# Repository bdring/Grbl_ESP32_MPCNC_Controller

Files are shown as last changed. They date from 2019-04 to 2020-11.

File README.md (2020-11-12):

# MPCNC Grbl_ESP32 Controller

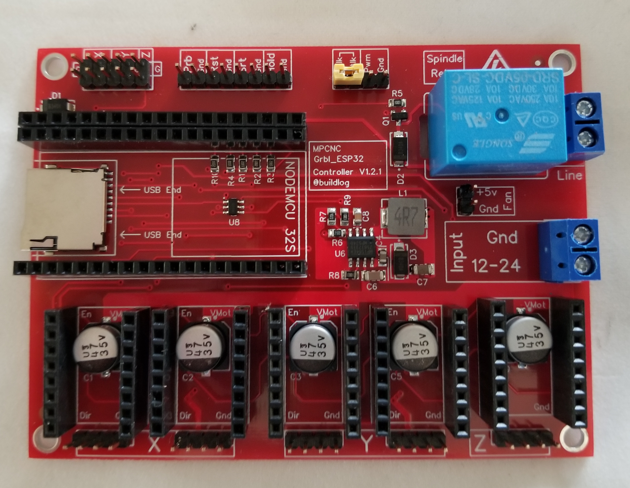
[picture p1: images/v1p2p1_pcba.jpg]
MPCNC Controller Image


This is a CNC controller specially designed to address the needs of the [MPCNC (Mostly Printed CNC) CNC Router](https://www.v1engineering.com/specifications/).

### Features

- ESP32 Microcontroller:
  - Very Fast: Dual core 32 bit, 240 MHz
  - Large Flash Memory
  - Wifi:
  - Bluetooth:
- Grbl_ESP32 Firmware:
  - Compatible with most existing Grbl gcode sender software.
  - Web User Interface
  - Multiple Interfaces
    - USB Serial:
    - Web User Interface:
    - Telnet:
    - Bluetooth:
    - SD Card:
- (5) Stepper Motor Drivers: On for each motor in the MPCNC design. Motors are ganging in firmware and have an auto squaring feature executed during homing.
- Limit Switch Connectors: 
- Control Pins:
- Spindle Control:
- Fan Power: 
- Micro SD card: 

### Getting One

They are available at the following links or you can source it yourself.

- [Tindie](https://www.tindie.com/products/33366583/grbl_esp32-mpcnc-cnc-controller/)

### Usage Instructions

[See the wiki](https://github.com/bdring/Grbl_ESP32_MPCNC_Controller/wiki)

### License

Creative Commons Attribution - ShareAlike 4.0 International

There are no commercial restrictions on using this design, but you must attribute the design to Bart Dring or @buildlog. You must also publish any changes or improvements to the design with the same open source license.  

### Version History

- Version 1.1 Original upload
- Version 1.2
  - Removed R/C filters on limit switches. This was not working for everyone. A firmware debouncing feature was added.
  - Made GPIO2 and output. Some dev modules have trouble with this as an input. Shuffled a few pins to accomodate this change. 
- Version 1.2.1
  - Changed orientation of relay for better layout
  - Removed pull down resistor on spindle PWM circuit (it was never installed previously)
  - Note: This uses the same cpu_map ans V1.2

### Source Files

- [Firmware](https://github.com/bdring/Grbl_Esp32)
- [DipTrace Source](https://github.com/bdring/Grbl_ESP32_MPCNC_Controller/tree/master/source)
- [Gerber Files](https://github.com/bdring/Grbl_ESP32_MPCNC_Controller/tree/master/gerbers)
- [Schematic](https://github.com/bdring/Grbl_ESP32_MPCNC_Controller/blob/master/gerbers/schematic.pdf)

### Donation

This project requires a lot of work and often expensive items for testing. Please consider a safe, secure and highly appreciated donation via the PayPal link below.



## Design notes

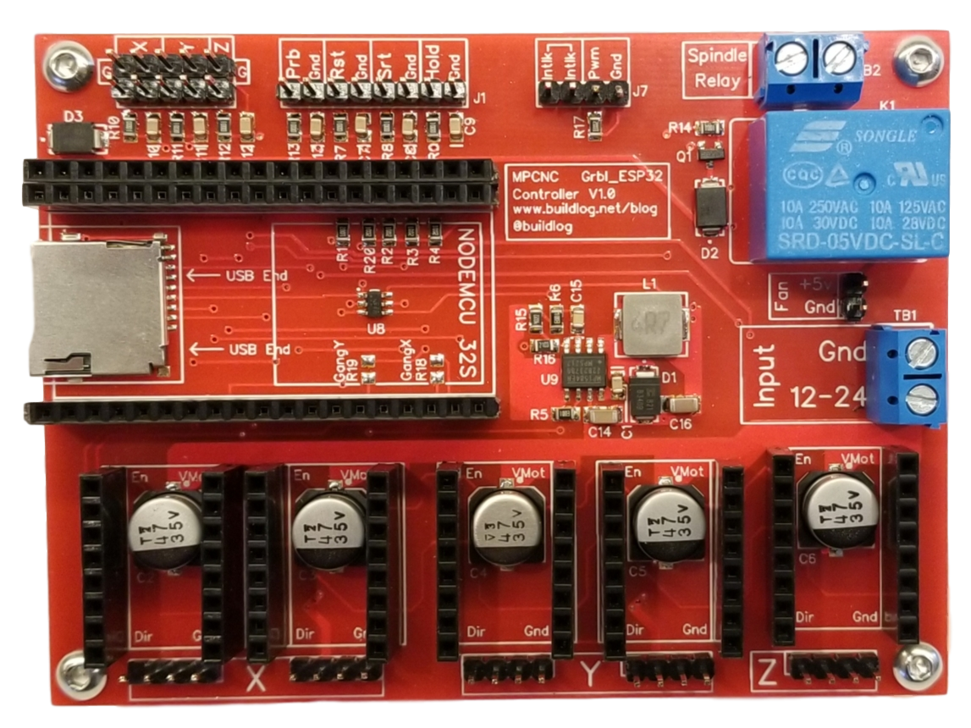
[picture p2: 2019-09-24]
images/v1p2_pcba.png

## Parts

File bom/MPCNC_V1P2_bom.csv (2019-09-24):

RefDes | Description | Value | Manufacturer | Mfg P/N | Link
C1, C2, C3, C5, C9 | Capacitor, Electrolytic | 47u 35V | Nichicon | UWX1V470MCL1GB | https://www.digikey.com/short/p80qq5
C1 | Capacitor, Ceramic | 100nF 50V | Kemet | C0805C104K5RACAUTO | https://lcsc.com/product-detail/Multilayer-Ceramic-Capacitors-MLCC-SMD-SMT_KEMET_C0805C104K5RACAUTO_100nF-104-10-50V-Car-level_C129641.html
C7 | Capacitor, Ceramic | 22uF 6.3V | Taiyo Yuden | JMK316BJ226KL-T | https://lcsc.com/product-detail/Multilayer-Ceramic-Capacitors-MLCC-SMD-SMT_TAIYO-YUDEN_JMK316BJ226KL-T_22uF-226-10-6-3V_C92791.html
C8 | Capacitor, Ceramic | 10uF | Taiyo Yuden | GMK316BJ106KL-T | https://lcsc.com/product-detail/Multilayer-Ceramic-Capacitors-MLCC-SMD-SMT_Taiyo-Yuden-GMK316BJ106KL-T_C92797.html
C15 | Capacitor, Ceramic | 150pF 50v 0805 | CCTC | TCC0805X7R151K500BT | https://lcsc.com/product-detail/Multilayer-Ceramic-Capacitors-MLCC-SMD-SMT_CCTC-TCC0805X7R151K500BT_C282743.html
D1, D2, D3 | Diode, Schottkey | diode, Schottkey 3A | (MDD) Jiangsu Yutai Elec | (MDD) Jiangsu Yutai Elec | https://lcsc.com/product-detail/Schottky-Barrier-Diodes-SBD_Jiangsu-Yutai-Elec-B340A_C64982.html
J1 | Connector, Header | Header Male 1x8 0.1" | Nextronics Engineering | Z-211-0811-0021-001 | https://lcsc.com/product-detail/Others_Nextronics-Engineering-Z-211-0811-0021-001_C190820.html
J2, J4, J6, J7, J9, J11 | Connector, Header | Header Male 1x4 0.1" | TE Connectivity |  | https://lcsc.com/product-detail/Male-Header_2-54mm-1-4P-HeaderG-FRegular_C152150.html
J3 | Connector, Header | Header Male 2x5 0.1" | Nextronics Engineering | Z-21310110021001 | https://lcsc.com/product-detail/PCB-Connectors-Headers-Male-Pins_Nextronics-Engineering-Z-21310110021001_C115170.html
J8 | Connector, Header | Header Male 1x2 0.1" | Nextronics Engineering | Z-211-0211-0021-001 | https://lcsc.com/product-detail/Male-Header_2-54mm-1-2P-Header-G-FRegular_C152154.html
J10 | Socket, Micro SD | Micro SD Socket | Korean Hroparts Elec TF-01A | TF-01A | https://lcsc.com/product-detail/Connector-Card-Sockets_Korean-Hroparts-Elec-TF-01A_C91145.html
K1 | Relay | Relay 5V SPDT | Ningbo Songle Relay | SRD-05VDC-SL-C | https://lcsc.com/product-detail/Relays_SRD-05VDC-SL-C_C35449.html
L1 | Inductor | Inductor 4.7uH 5.5A | Chilisin Elec | MHCI06030-4R7M-R8 | https://lcsc.com/product-detail/Power-Inductors_Chilisin-Elec-MHCI06030-4R7M-R8_C108295.html
Q1 | Transistor | NPN Transistor 0.5A | Semtech | MMBT9013H | https://lcsc.com/product-detail/Transistors-NPN-PNP_MMBT9013H_C81408.html
R1, R2, R3, R4, R10 | Resistor | 10k | YAGEO | AC0805FR-0710KL | https://lcsc.com/product-detail/Chip-Resistor-Surface-Mount_10KR-1002-1_C140868.html
R5 | Resistor | 1K | YAGEO | AC0805FR-071KL | https://lcsc.com/product-detail/Chip-Resistor-Surface-Mount_1KR-1001-1_C140870.html
R6 | Resistor | 210k | YAGEO | AC0805FR-07210KL | https://lcsc.com/product-detail/Others_YAGEO-AC0805FR-07210KL_C228629.html
R7 | Resistor | 40.2k | YAGEO | AC0805FR-0740K2L | https://lcsc.com/product-detail/Others_YAGEO-AC0805FR-0740K2L_C228820.html
R8, R9 | Resistor | 100k | YAGEO | AC0805FR-07100KL | https://lcsc.com/product-detail/Chip-Resistor-Surface-Mount_100KR-1003-1_C144587.html
TB1, TB2 | Terminal Block | Terminal Block 1x2 5mm Blue | Aliexpress |  | https://www.aliexpress.com/item/Free-Shipping-5-08-301-2P-301-2P-500PCS-2-Pin-Screw-Terminal-Block-Connector-5mm/1681835880.html
U1, J9 | Connector, Header | ESP-32 Header Female 1x19 0.1" |  |  | https://www.aliexpress.com/item/100Pcs-Per-Lot-2-54mm-Pitch-1x19-Pin-19-Pin-Female-Single-Row-Straight-Header-Strip/32760221364.html
U2, U3, U4, U5, U7 | Connector, Header | Header Female 1x8 0.1" |  |  | https://lcsc.com/product-detail/Female-Header_2-54mm-1-8P-Straight-Female-header_C27438.html
U6 | DC-DC Power Supply Controller | MP1584EN | Monolithic Power Systems | MP1584EN-LF-Z | https://lcsc.com/product-detail/DC-DC-Converters_MPS_MP1584EN-LF-Z_MP1584EN-LF-Z_C15051.html
U8 | Voltage level Shifter | TXS0101DBVR | TI | TXS0101DBVR | https://lcsc.com/product-detail/Logic-ICs_TI_TXS0101DBVR_TXS0101DBVR_C132604.html

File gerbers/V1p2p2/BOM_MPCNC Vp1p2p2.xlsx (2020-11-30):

RefDes | Value | Quantity | SMD | Thru Hole | Manufacturer | Mfg P/n | Link
C1, C2, C3, C5, C9 | 47u 35V | 5 | 5 |  | Nichicon | UWX1V470MCL1GB | https://www.digikey.com/short/ptwvbr
C4, C10, C11, C12, C13, C14, C15, C16 | 100nF | 8 | 8 |  | Kemet | C0805C104K5RACAUTO | https://lcsc.com/product-detail/Multilayer-Ceramic-Capacitors-MLCC-SMD-SMT_KEMET_C0805C104K5RACAUTO_100nF-104-10-50V-Car-level_C129641.html
C6 | 10uF | 1 | 1 |  | Taiyo Yuden | GMK316BJ106KL-T | https://lcsc.com/product-detail/Multilayer-Ceramic-Capacitors-MLCC-SMD-SMT_Taiyo-Yuden-GMK316BJ106KL-T_C92797.html
C7 | 22uF 6.3V | 1 | 1 |  | Taiyo Yuden | JMK316BJ226KL-T | https://lcsc.com/product-detail/Multilayer-Ceramic-Capacitors-MLCC-SMD-SMT_TAIYO-YUDEN_JMK316BJ226KL-T_22uF-226-10-6-3V_C92791.html
C8 | 150pF | 1 | 1 |  | CCTC | TCC0805X7R151K500BT | https://lcsc.com/product-detail/Multilayer-Ceramic-Capacitors-MLCC-SMD-SMT_CCTC-TCC0805X7R151K500BT_C282743.html
D1, D2, D3 | Diode, Schottkey 3A | 3 | 3 |  | (MDD) Jiangsu Yutai Elec | (MDD) Jiangsu Yutai Elec | https://lcsc.com/product-detail/Schottky-Barrier-Diodes-SBD_Jiangsu-Yutai-Elec-B340A_C64982.html
J1 | Header Male 1x8 0.1" | 1 |  | 1 | Nextronics Engineering | Z-211-0811-0021-001 | https://lcsc.com/product-detail/Others_Nextronics-Engineering-Z-211-0811-0021-001_C190820.html
J2, J4, J6, J7, J9, J11 | Header Male 1x4 0.1" | 5 |  | 5 |  |  | https://lcsc.com/product-detail/Male-Header_2-54mm-1-4P-HeaderG-FRegular_C152150.html
J3 | Header Male 2x5 0.1" | 1 |  | 1 | MINTRON | MTP125-1205S1 | https://lcsc.com/product-detail/Pin-Header-Female-Header_MINTRON-MTP125-1205S1_C358694.html
J8 | Male Header 1x2 0.1" | 1 |  | 1 | MINTRON | MTP125-1102S1 | https://lcsc.com/product-detail/Pin-Header-Female-Header_MINTRON-MTP125-1102S1_C358684.html
J10 | Micro SD Socket | 1 |  | 1 | Korean Hroparts Elec TF-01A | TF-01A | https://lcsc.com/product-detail/Connector-Card-Sockets_Korean-Hroparts-Elec-TF-01A_C91145.html
K1 | Relay 5VDC SPDT | 1 |  | 1 | Ningbo Songle Relay | SRD-05VDC-SL-C | https://lcsc.com/product-detail/Relays_Ningbo-Songle-Relay-SRD-05VDC-SL-C_C35449.html
L1 | 4.7uH | 1 | 1 |  | Chilisin Elec | MHCI06030-4R7M-R8 | https://lcsc.com/product-detail/Power-Inductors_Chilisin-Elec-MHCI06030-4R7M-R8_C108295.html
Q1 |  | 1 | 1 |  | Nexperia | BCV26,215 | https://lcsc.com/product-detail/Darlington-Transistors_Nexperia_BCV26-215_BCV26-215_C130420.html
R1, R2, R3, R4, R10 | 10k | 5 | 5 |  | YAGEO | AC0805FR-0710KL | https://lcsc.com/product-detail/Chip-Resistor-Surface-Mount_10KR-1002-1_C140868.html
R5 | 1K | 1 | 1 |  | YAGEO | AC0805FR-071KL | https://lcsc.com/product-detail/Chip-Resistor-Surface-Mount_1KR-1001-1_C140870.html
R6 | 210k | 1 | 1 |  | YAGEO | AC0805FR-07210KL | https://lcsc.com/product-detail/Others_YAGEO-AC0805FR-07210KL_C228629.html
R7 | 40.2k | 1 | 1 |  | YAGEO | AC0805FR-0740K2L | https://lcsc.com/product-detail/Others_YAGEO-AC0805FR-0740K2L_C228820.html
R8, R9 | 100k | 2 | 2 |  | YAGEO | AC0805FR-07100KL | https://lcsc.com/product-detail/Chip-Resistor-Surface-Mount_100KR-1003-1_C144587.html
R11, R12, R13, R14, R15, R16, R17 | 100R | 7 | 7 |  | YAGEO | AC0805FR-07100RL | https://lcsc.com/product-detail/Chip-Resistor-Surface-Mount_100R-100R-1_C138274.html
TB1, TB2 |  | 2 |  | 2 | DIBO | DB301V-5.0-2P | https://lcsc.com/product-detail/Screw-terminal_DIBO-DB301V-5-0-2P_C395882.html
U1,J5 | 1x19 Female Header 8.5mm Tall | 3 |  | 3 | 1x19 Female Header |  | https://www.aliexpress.com/item/100Pcs-Per-Lot-2-54mm-Pitch-1x19-Pin-19-Pin-Female-Single-Row-Straight-Header-Strip/32760221364.html
U2, U3, U4, U5, U7 | 1x8 Female Header 8.5mm Tall | 10 |  | 10 | 1x8 Female Header |  | https://lcsc.com/product-detail/Female-Header_2-54mm-1-8P-Straight-Female-header_C27438.html
U6 | MP1584EN | 1 | 1 |  | Monolithic Power Systems | MP1584EN-LF-Z | https://lcsc.com/product-detail/DC-DC-Converters_MPS_MP1584EN-LF-Z_MP1584EN-LF-Z_C15051.html
U8 | TXS0101DBVR | 1 | 1 |  | TI | TXS0101DBVR | https://lcsc.com/product-detail/Logic-ICs_TI_TXS0101DBVR_TXS0101DBVR_C132604.html
 |  |  | 40 | 25

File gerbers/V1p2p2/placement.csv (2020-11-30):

RefDes | Name | Pattern | X (in) | Y (in) | Side | Rotate | Value
C1 |  | CAPAE-8.35x8.35h6.2 | 0.55 | 0.774 | Top | 270 | 47u 35V
C2 |  | CAPAE-8.35x8.35h6.2 | 1.25 | 0.774 | Top | 270 | 47u 35V
C3 |  | CAPAE-8.35x8.35h6.2 | 2 | 0.774 | Top | 270 | 47u 35V
C4 | CAP_0805 | CAP_0805 | 2.4927 | 1.3852 | Top | 270 | 100nF
C5 |  | CAPAE-8.35x8.35h6.2 | 2.7 | 0.774 | Top | 270 | 47u 35V
C6 | CAP_NP_1206 | CAP_1206 | 2.4266 | 1.2567 | Top | 180 | 10uF 35V
C7 | CAP_NP_1206 | CAP_1206 | 2.7676 | 1.3 | Top | 0 | 22uF 6.3V
C8 | CAP_NP_1206 | CAP_0805 | 2.3167 | 1.675 | Top | 90 | 150pF
C9 |  | CAPAE-8.35x8.35h6.2 | 3.45 | 0.824 | Top | 270 | 47u 35V
D1 | 10BQ100 | b340a-13-f | 0.1699 | 2.4641 | Top | 0
D2 | 10BQ100 | b340a-13-f | 2.6188 | 2.16 | Top | 90
D3 | 10BQ100 | b340a-13-f | 2.6097 | 1.3578 | Top | 270
FD1 | Fiducial-1-3mm | Fiducial-1-3mm | 0.1378 | 0.315 | Top | 90
FD2 | Fiducial-1-3mm | Fiducial-1-3mm | 3.622 | 2.7756 | Top | 90
J1 | HDR-1x8 | HDR-1x8 | 1.45 | 2.65 | Top | 0 | Header Male 1x8 0.1
J2 |  | HDR-1x4 | 0.55 | 0.15 | Top | 0 | Header Male 1x4 0.1
J3 | HDR-2x5 | HDR-2x5 | 0.6 | 2.7 | Top | 0 | Header Male 2x5 0.1
J4 |  | HDR-1x4 | 1.25 | 0.15 | Top | 0 | Header Male 1x4 0.1
J5 | HDR-1x19 | HDR-1x19 | 1 | 2.3 | Top | 0
J6 |  | HDR-1x4 | 2 | 0.15 | Top | 0 | Header Male 1x4 0.1
J7 |  | HDR-1x4 | 2.7 | 0.15 | Top | 0 | Header Male 1x4 0.1
J8 | HDR-1x2 | HDR-1x2 | 3.075 | 1.7813 | Top | 270 | Header Male 1x2 0.1
J9 |  | HDR-1x4 | 3.425 | 0.15 | Top | 0 | Header Male 1x4 0.1
J10 | TF-01A | TF-01A | 0.3006 | 1.752 | Top | 0 | Micro SD Socket
J11 |  | HDR-1x4 | 2.35 | 2.65 | Top | 0 | Header Male 1x4 0.1
K1 | JS-M1-9V-5 | JS-M | 3.1705 | 2.2519 | Top | 90 | Relay 5V SPDT
L1 | IND_1210 | Inductor 06030 | 2.6506 | 1.6614 | Top | 0 | 4.7uH
Q1 | MMBT9014 | TO-236 | 2.6188 | 2.3856 | Top | 180
R1 | RES_0805 | RES_0805 | 1.5 | 2.0626 | Top | 270 | 10k
R2 | RES_0805 | RES_0805 | 1.6 | 2.0626 | Top | 270 | 10k
R3 | RES_0805 | RES_0805 | 1.7 | 2.0626 | Top | 270 | 10k
R4 | RES_0805 | RES_0805 | 1.4125 | 2.0624 | Top | 270 | 10k
R5 | RES_0805 | RES_0805 | 2.6124 | 2.4938 | Top | 0 | 1K
R6 | RES_0805 | RES_0805 | 2.1721 | 1.5596 | Top | 0 | 210k
R7 | RES_0805 | RES_0805 | 2.1347 | 1.6782 | Top | 270 | 40.2k
R8 | RES_0805 | RES_0805 | 2.2631 | 1.2606 | Top | 0 | 100k
R9 | RES_0805 | RES_0805 | 2.2257 | 1.675 | Top | 90 | 100k
R10 | RES_0805 | RES_0805 | 1.3 | 2.0624 | Top | 90 | 10k
TB1 | TB_5mm_2POS | TB_5mm_2POS | 3.8125 | 2.3438 | Top | 270
TB2 | TB_5mm_2POS | TB_5mm_2POS | 3.75 | 1.525 | Top | 270
U1 | ESP-32 NodeMCU 32S | ESP-32 NodeMCU 32S | 0.1 | 2.2 | Top | 270 | ESP-32
U2 | StepStick | StepStick | 0.3 | 1 | Top | 0
U3 | StepStick | StepStick | 1 | 1 | Top | 0
U4 | StepStick | StepStick | 1.75 | 1 | Top | 0
U5 | StepStick | StepStick | 2.45 | 1 | Top | 0
U6 | MP1584EN | MP1584EN | 2.3425 | 1.4551 | Top | 180 | MP1584EN
U7 | StepStick | StepStick | 3.2 | 1.05 | Top | 0
U8 | TXS0101DBVR | SOT23-6 | 1.4344 | 1.7501 | Top | 0 | TXS0101DBVR
C10 | CAP_0805 | CAP_0805 | 0.5 | 2.5187 | Top | 90 | 100nF
C11 | CAP_0805 | CAP_0805 | 0.7 | 2.5187 | Top | 90 | 100nF
C12 | CAP_0805 | CAP_0805 | 0.8938 | 2.5187 | Top | 90 | 100nF
R14 | RES_0805 | RES_0805 | 1.1 | 2.5187 | Top | 270 | 100
R15 | RES_0805 | RES_0805 | 1.3 | 2.5187 | Top | 270 | 100
R11 | RES_0805 | RES_0805 | 0.4 | 2.5187 | Top | 270 | 100
R12 | RES_0805 | RES_0805 | 0.6 | 2.5187 | Top | 270 | 100
R13 | RES_0805 | RES_0805 | 0.8 | 2.5187 | Top | 270 | 100
R16 | RES_0805 | RES_0805 | 1.5 | 2.5187 | Top | 270 | 100
R17 | RES_0805 | RES_0805 | 1.7 | 2.5187 | Top | 270 | 100
C13 | CAP_0805 | CAP_0805 | 1.2 | 2.5187 | Top | 90 | 100nF
C14 | CAP_0805 | CAP_0805 | 1.4 | 2.5187 | Top | 90 | 100nF
C15 | CAP_0805 | CAP_0805 | 1.6 | 2.5187 | Top | 90 | 100nF
C16 | CAP_0805 | CAP_0805 | 1.8 | 2.5187 | Top | 90 | 100nF

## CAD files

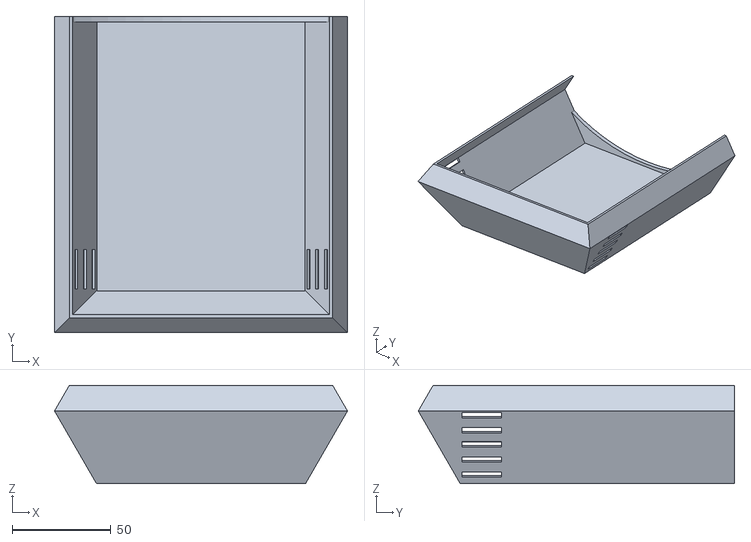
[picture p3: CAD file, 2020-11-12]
stl/Grbl_ESP-32 MPCNC Case Lid.stl
148.3 x 160.2 x 49.8

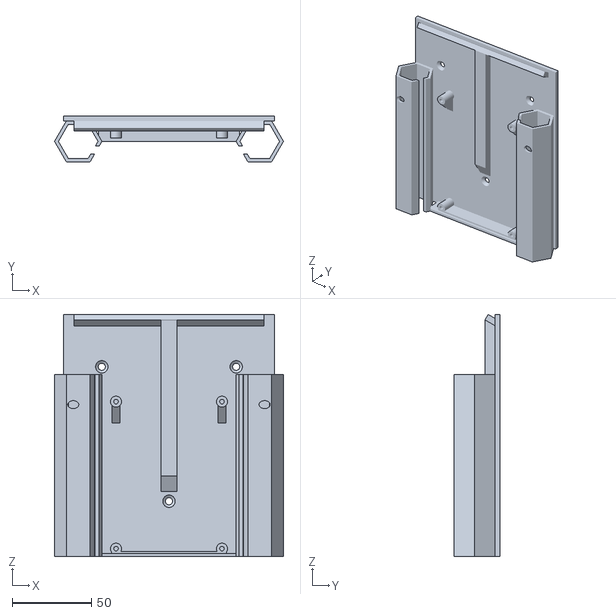
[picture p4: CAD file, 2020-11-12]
stl/Grbl_ESP-32 MPCNC Case Flat Base.stl
144.8 x 29.0 x 153.1

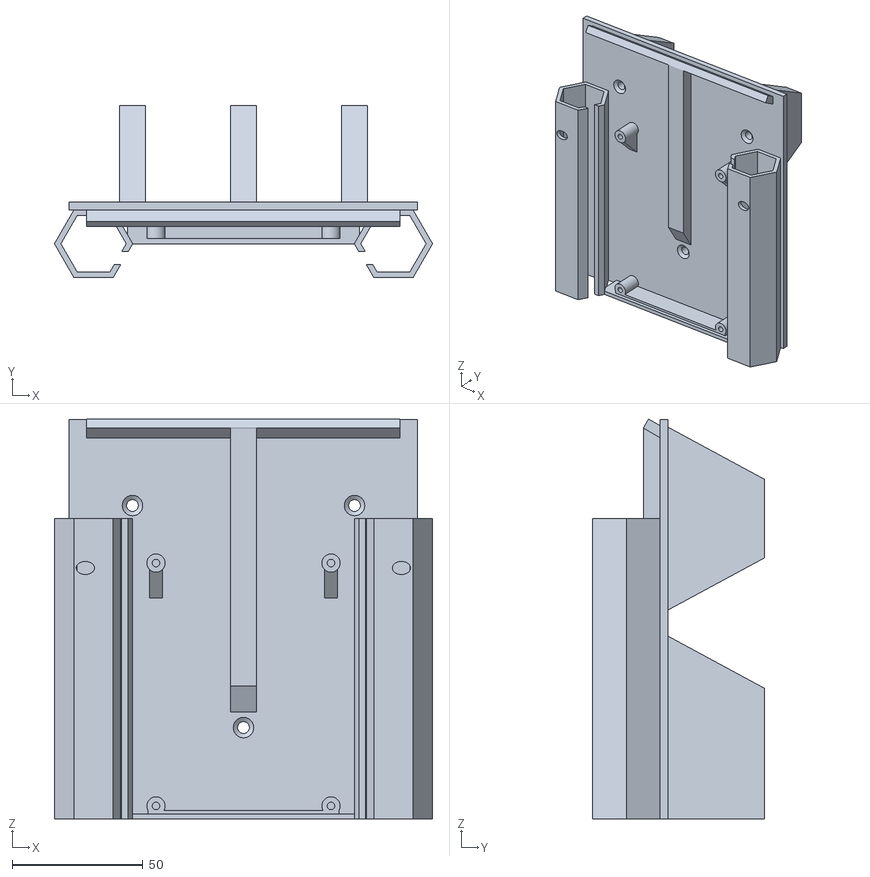
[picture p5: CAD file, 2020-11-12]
stl/Grbl_ESP-32 MPCNC Case Standoff Base.stl
144.8 x 66.0 x 153.1

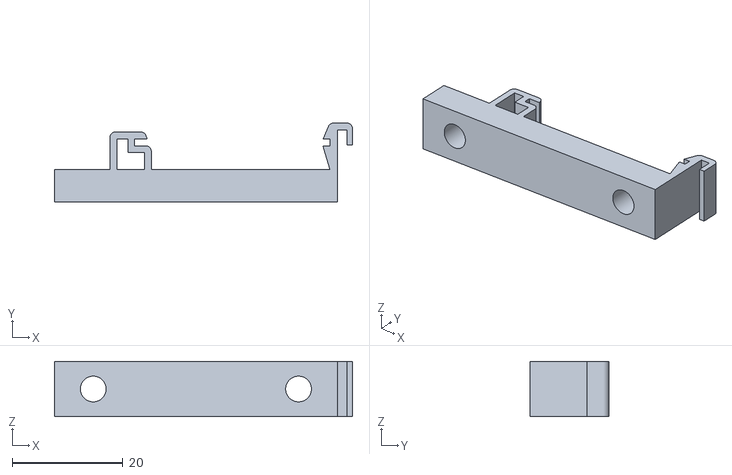
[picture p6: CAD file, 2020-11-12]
stl/DINRailClip.stl
53.8 x 14.3 x 10.0

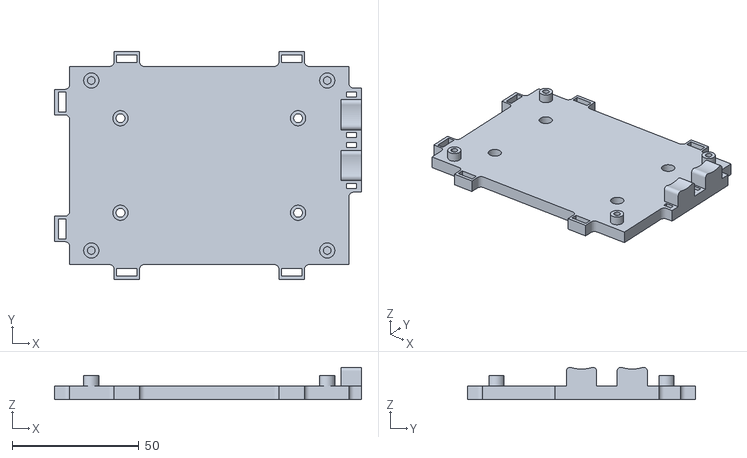
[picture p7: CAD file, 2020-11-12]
stl/GRBLESP32MPCNCDinRailPlate.stl
121.0 x 90.0 x 12.8

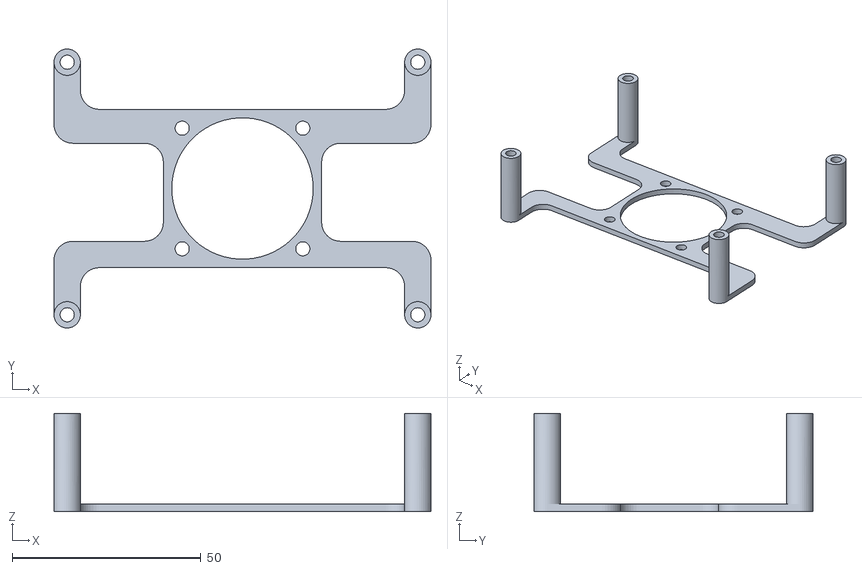
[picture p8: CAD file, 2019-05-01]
stl/mpcnc_fan_mount.stl
100.0 x 74.0 x 26.0

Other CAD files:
stl/Grbl_ESP-32 MPCNC Case Lid Holes.stl

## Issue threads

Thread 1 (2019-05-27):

Only one motor per axis moving

gmihovics, 2019-05-27:
I just finished wiring the four X and Y steppers and limit switches for my MPCNC. When trying to move either axis, only the second of the motors for that axis move. So if I move the X axis, only X2 moves, Y2 for Y.

I swapped the motors and drivers (A4988) to make sure all the components work and they do. I also went ahead and recompiled the firmware as per the wiki with no change.

I unfortunately do not have an oscilloscope or logic analyser so I can't verify the board is sending steps to both motors.

Am I overlooking something?

bdring, 2019-05-27:
My first guess is you are using the wrong cpu_map. You need to use CPU_MAP_MPCNC.

[See this page about that](https://github.com/bdring/Grbl_ESP32_MPCNC_Controller/wiki).

gmihovics, 2019-05-27:
Thanks for he quick reply. I unfortunately followed those instructions when I recompiled the firmware.

bdring, 2019-05-27:
I just checked the latest firmware to make sure there are no issues no issues crept in recent updates.

It works fine for me.  Can you double check all to solder joints?

You could try swapping the pins in cpu_map.h on the x axis motors to see if it is a firmware or hardware issue, like this....

#define X_STEP_PIN      GPIO_NUM_22   // was GPIO_NUM_12
#define X_STEP_B_PIN    GPIO_NUM_12 // was GPIO_NUM_22

If only one motors spins, but it is now the other one, it would appear to be a firmware issue.
If the same motors as before spins, it is likely a hardware issue.

gmihovics, 2019-05-27:
That's a good idea, I will try that when I get home today.

gmihovics, 2019-05-27:
So I have reconfigured the pins and uploaded the firmware like you suggested. I checked before and after and both times the same motor moved.

Here is the relevant code

`config.h`
```
#ifndef config_h
#define config_h
#include "grbl.h" // For Arduino IDE compatibility.

//#define ESP_DEBUG

// Define CPU pin map and default settings.
// NOTE: OEMs can avoid the need to maintain/update the defaults.h and cpu_map.h files and use only
// one configuration file by placing their specific defaults and pin map at the bottom of this file.
// If doing so, simply comment out these two defines and see instructions below.
#define DEFAULTS_GENERIC

//#define CPU_MAP_ESP32 // these are defined in cpu_map.h
#define CPU_MAP_MPCNC

#define VERBOSE_HELP // adds addition help info, but could confuse some senders
```

`cpu_map.h`
```
#define USE_GANGED_AXES // allow two motors on an axis

//#define X_STEP_PIN      GPIO_NUM_12
//#define X_STEP_B_PIN    GPIO_NUM_22	 // ganged motor
#define X_STEP_PIN GPIO_NUM_22 // was GPIO_NUM_12
#define X_STEP_B_PIN GPIO_NUM_12 // was GPIO_NUM_22

#define X_AXIS_SQUARING
```

I have also confirmed the the other motor works if i swap them as well as the drivers. The soldering looks well done, you sent a really nice board. I am not sure what is going on.

bdring, 2019-05-27:
Thanks for doing that. It helps narrow things down.  Does the non moving motor lock (resist manual turning) when the other motor moves?

Make sure $1=255 to keep it locked.

gmihovics, 2019-05-28:
Ok so interesting results. I verified $1 == 255. I also unplugged the good motors and told the board to move the X and Y axis. Like usual I got no movement but I can verify the other motors are energised. I am able to move them by hand but they have significant resistance compared to the unplugged motors and you can feel the skipping steps when you force them.

gmihovics, 2019-05-28:
I wrote a test program that stepped gpio 22 and it would spin the motor attached just fine. When I change it to pin 12, it does not.

bdring, 2019-05-28:
Do you have a volt meter? Can you slowly toggle the pins while looking at the pins?  Measure at the ESP32 and the motor driver

You could have some dead pins on the ESP32. Is there a chance a motor driver was ever installed backwards or off a pin? Was the ESP32 ever used on another project?

gmihovics, 2019-05-28:
I got the ESP32 with the board so I assume it was new. I also made sure I put the drivers in properly each time.

I'll try to measure the voltage in a bit and let you know how it works. I was also thinking I might grab one of my ramps boards and jumper the step and direction pins to the grbl board. That should also tell us if it's the ESP32 or not.

bdring, 2019-05-28:
I found and issue. These 2 rows of pins are supposed to be connected, but I found an open circuit between these 2.

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

Here is the Gerber

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

I am not sure how this happened, but I probably made a mistake somewhere at the last revision when I made the gerber files.

I have been testing using the narrower ESP32 and assumed the connections were OK.

If you could solder a wire vertically between the pins, that should fix it. I can replace the board with a repaired board if you would rather have me do it.

gmihovics, 2019-05-28:
Removing the ESP32 seems to have killed it, it no longer registers as a device in my system so I am unable to access it. I'll have to use another board like my ramps to test out the carrier board.

gmihovics, 2019-05-28:
Ok, I'll confirm the open traces and fix them on my board. I'll then carry on with my test to verify.

Good find.

gmihovics, 2019-05-28:
I decided to run the ESP32 under my hot air reflow and it fixed whatever bad connection there was so we are back in business.

I reflashed the firmware onto the ESP32 and then added the soldering bridges as you said. Plugged the ESP32 back into the board and powered it all up. The light comes on but no web interface or serial data on the monitor. If I take the ESP32 out of the carrier board I can get the web interface and serial data on the monitor but the moment I plug it into the carrier again, nothing.

I went ahead and removed the solder bridges that I made but now I am having the same issue again where I can't get the web interface or data on the serial monitor. Interestingly though, I get this error when trying to flash the ESP32 in the carrier:

```
Changing baud rate to 512000
Changed.
Configuring flash size...
Warning: Could not auto-detect Flash size (FlashID=0xffffff, SizeID=0xff), defaulting to 4MB
Compressed 16848 bytes to 10928...

A fatal error occurred: Timed out waiting for packet content
```

Searching `Warning: Could not auto-detect Flash size` brought me to this answer on another issue https://github.com/espressif/esptool/issues/305#issuecomment-387598276

Apparently GPIO12 can cause issues with the internal flash if it is pulled high. I can't see any reason it should be high and I have re-soldered all the pins on the carrier board to make sure there is no short but I still can't get it to run properly on the carrier board any more.

here is the flashing working when pulled out of the carrier board for reference

```
Changing baud rate to 512000
Changed.
Configuring flash size...
Auto-detected Flash size: 4MB
Compressed 16848 bytes to 10928...
Wrote 16848 bytes (10928 compressed) at 0x00001000 in 0.2 seconds (effective 575.5 kbit/s)...
Hash of data verified.
Compressed 3072 bytes to 143...
Wrote 3072 bytes (143 compressed) at 0x00008000 in 0.0 seconds (effective 3225.7 kbit/s)...
Hash of data verified.
Compressed 8192 bytes to 47...
Wrote 8192 bytes (47 compressed) at 0x0000e000 in 0.0 seconds (effective 11874.8 kbit/s)...
Hash of data verified.
Compressed 1778384 bytes to 1055467...
Wrote 1778384 bytes (1055467 compressed) at 0x00010000 in 23.0 seconds (effective 618.6 kbit/s)...
Hash of data verified.

Leaving...
Hard resetting via RTS pin...
```

bdring, 2019-05-28:
I have done dozens of ESP32 projects using both the narrow and wide version.

With the narrow version I almost always get the issue where I have to hold the boot button to load firmware.

With the wide version, I never have to hold the boot button, but I have seen the issue where it won't program in the socket, but runs fine.

I prefer the wide version because the problem is rare and I tend to wirelessly upload firmware after the first load. I always do the first load out of the socket for IO safety.

The wide version also does not have the LED on IO2 which makes that pin easier to use.

gmihovics, 2019-05-28:
Ok I'll have to order a new ESP32 DEVKITC V4 module then. It just will not run in the board any more. I guess we can close this and I'll open a new issue if the new ESP32 gets here and has the same issue.

bdring, 2019-05-28:
OK, I am happy to help in real time [via Slack](https://join.slack.com/t/buildlog/shared_invite/enQtNjEzNjMwMTA3ODQ2LTJlYjgxYzY1NmE1ZGI2OGQ0NmVmNWU3NzhmNmUwMjBjMTFhNjk1NGE5OWVhMDk0NmIzNTI4NGE5NTE2ZTVlZDE) as well.

Closed 2019-05-28.

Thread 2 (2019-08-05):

more flexible support for stepstick modules

davidelang, 2019-08-05:
In the next revision, could you provide support for more advanced stepper modules?

this would require that the three config pins have a way to set them individually or have them connect to spi (for the most advanced features)

If this could support the tmc2130 modules, you could potentially eliminate limit switches.

I'm thinking of a 3 pin jumper for each of the config pins, high, low (one side connected or removed) or spi (other side connected)

bdring, 2019-08-05:
I have other Grbl_ESP32 boards with SPI driver support. It can use a lot of extra I/O. You need a Chip Select pin for each driver.

I have a test board that uses one CS pin for all drivers. It works, but requires modifications to the standard library. Those mods are write only at this time. It does allow you to setup all features.

bdring, 2019-08-05:
Here are some photos of that controller.

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

dvisser, 2019-08-05:
@bdring can you share the artwork for this board variant please? possibly as a new branch called "trinamic" or "spi" or similar? even just the schematic would suffice, as I dont use diptrace (mainly KiCAD or Altium).

dvisser, 2019-08-05:
and are you still daisy-chaining the trinamic modules? (ie. all 4 of them use a single CS line?)

bdring, 2019-08-05:
OK. I am out of town, so it will take a day or so.

I have a few extras assembled. I would be willing to part with one, but only to seasoned programmers, that can help move this forward.

dvisser, 2019-08-06:
I dont expect a handout of hardware mate, please share the design and I can spin my own board up if need be, happy to assist with firmware if needed also.

bdring, 2019-08-06:
Attached is the schematic.

I am away from my office until Aug 20th on vacation. I do not have time to create a proper repo for the controller.

I can send the gerbers via email or [Slack](https://join.slack.com/t/buildlog/shared_invite/enQtNjEzNjMwMTA3ODQ2LTZkMTE5MjcwZTY4MjgwOWEwMWE1MzZlNGNhNDdmMWEwNWZkN2Y5NjBlNjBlZjY2MTg3ZThlN2I3YjEwMzUyMWI), but I do not want to publicly post them without well documented repo.

The controller uses [this branch of Grbl_ESP32](https://github.com/bdring/Grbl_Esp32/tree/TMCStepper). It requires this fork of the [TMCStepper Library](https://github.com/bdring/TMCStepper) for daisy chain support.

Currently you can only write to the drivers. I have some code to read, but I have not tested it at all and I am sure it does not work yet.

To save pins, the SPI data lines are shared with the SD card. The SD has its own CS and the drivers share a CS. You must install 4 drivers or jumper the data through any missing drivers.

[SPI_4Axis_V1_Schm.pdf](https://github.com/bdring/Grbl_ESP32_MPCNC_Controller/files/3472112/SPI_4Axis_V1_Schm.pdf)

dvisser, 2019-08-06:
OK not a problem, I will take a look. Thank you for sharing.

dvisser, 2019-08-07:
What are the currently "working" methods of receiving grbl strings? wifi-serial, usb cable, read g-code file from sd card, etc? Cant really tell from what I have read (without reading through the source, which I will be doing) where you are roughly up to?

dvisser, 2019-08-07:
nevermind the above, I read the WiKi properly :-)

bdring, 2019-08-07:
We treat the communications methods as separate channels. If Bluetooth asks for status, only Bluetooth gets the status.

The serial port is treated as the debugging port because it is always there and survives a reboot. You do not loose the connection during reboot. A lot of  startup info and debugging is sent there.

See grbl_send(...) and grbl_sendf(...) for more info.

dvisser, 2019-08-07:
OK Thank you

bdring, 2019-08-12:
@dvisser

Repo created

https://github.com/bdring/4_Axis_SPI_CNC

davidelang, 2019-08-12:
I was hoping for something with 5 axis support (looking at the lowrider 2)

bdring, 2019-08-12:
Maybe you should offer a bounty :-)

dvisser, 2019-08-13:
thank you bdring, I will check it all out now.

dvisser, 2019-08-20:
I have designed my own PCB to use your TMCStepper branch of firmware.
It can be found here if you are interested, I have referenced you accordingly.
https://github.com/dvisser/NodeMCU-ESP-32S-3-Axis-CNC-Controller

bdring, 2019-08-20:
That looks good.

While the output of the spindle is PWM, it is on one of the ESP32s 8-bit DAC pins. With a small firmware change, you might be able to simplify your spindle circuit a little.

dvisser, 2019-08-20:
it is still a work in progress, but thank you. I am very much used to Altium Designer (over 10years experience) and still learning KiCAD.

I wasnt aware we had a DAC peripheral, that does sound interesting and is worth looking into, it would remove the need for the PWM to analog DAC IC I was planning to use.

dvisser, 2019-08-20:
please could you invite me to your slack workspace (never used slack, but keen to see what it is like)

d.visser@vizztech.com.au

bdring, 2019-08-20:
The option to output DAC or PWM might make your board more flexible to use other speed controllers.

invite sent

dvisser, 2019-08-20:
indeed, so might be worth keeping the current hardware configuration I guess.

Just joined slack also. Thank you.

davidelang, 2019-09-02:
what sort of bounty would get attention?

dvisser, 2019-09-02:
@davidelang ??

davidelang, 2019-09-02:
you mentioned a few posts up that I should consider posting a bounty to get a 5+
axis controller that would support the smart stepper modules, how big a bounty
are you talking about?

I understand the argument that homing isn't that important for a CNC, but for
something like the MPCNC or the lowrider2, it's especially easy to get the two
sides out of sync with each other and have the machine be racked. So having the
ability to run against a stop as a squaring routine (potentially slightly
different than a homing routine) is something I find attractive.

I have this problem on my dual Y 3d printer where the two sides can get out of
sync when I transport it, and the lowrider seems especially sensitive to this
problem.

so something that can drive 2130 or 2209 modules so that it can just run against
limits rather than having to wire endstops is attractive. (long endstop wires
close to electrically noisy routers isn't a great match)

David Lang

dvisser, 2019-09-02:
If using 2130's or 2209's you could use stallguard whilst homing/crashing to square up the axis. Pretty simple. I can assist with code if needed, but this is bdring's party :-)

davidelang, 2019-09-02:
On Mon, 2 Sep 2019, Dan Visser wrote:

> If using 2130's or 2209's you could use stallguard whilst homing/crashing to
> square up the axis. Pretty simple. I can assist with code if needed, but this
> is bdring's party :-)

That's exactly what I'm hoping for, but before you can write the code for it,
you have to have a way to communicate ith the 2130/2209

David Lang

dvisser, 2019-09-02:
@bdring I got my PCB's today!

https://ibb.co/B3tv83b

dvisser, 2019-09-02:
@davidelang  bdring's firmware (Tmcstepper branch I believe) already talks to daisy chained 2130's. Only one way at present. I have code that I have forked that does both ways. I bet he isn't far off either. I could always put a pull request in once my code is polished anyway. But you could use bdring's FW and simply set the diag1 pin to toggle on trigger of stallguard and connect that to you relevant axis limit SW input pin.

bdring, 2019-09-02:
My branch only writes in daisy chain mode. I worked a little on daisy chain reading, but never finished it.

Setting up stallgaurd is tricky, especially if you have long stepper wires. You are trying to measure power losses in the motor coils. If you have wiring losses, that needs to be "tuned" out. Also, stallgaurd does not work well (false or missed stalls) at very low or very high speeds.  You typically need to tell stallgaurd the speed window where it should trigger the stallgaurd signal.

You need to be able view a fast stream of stallgaurd data to do that tuning.  Reading is needed for that. Also Grbl is not a very good platform for tuning. You want a program that runs the motor at a constant speed for long periods of time and has the ability to adjust the speed and tuning values on the fly.

I ended up making a separate program for tuning and just loading the tuning values into Grbl.

davidelang, 2019-09-03:
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

stupid question, would it make sense to put the stepstick module closer to the
motor and have the long wires on the CPU side of the module?

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

interesting, thanks for the info

bdring, 2019-09-03:
It is probably not better to extend the signals to the driver. Those are sensitive pins and are easily damaged with ESD that could be picked up over long wires.

My point was....You will need to tune any setup. so you need the read capability and firmware that helps you do it.

On my wall plotter project, one small NEMA17 was right next to the driver and one was about 8 feet away from the driver connected by a CAT5E (not ideal) cable. The two motors had significantly different tuning, but they both detected stalls fine.

One other thing to keep in mind. Stallgaurd will, at best, detect to about the nearest 1/2 step. On a machine like an MPCNC using 20 tooth GT2 pulleys (40mm/rev) , you are looking at +/0.1mm detection at best. A simple microswitch will do much better.

If you are just homing the machine before a job, that is fine, but if you are looking for reputability for fixtures, I would be concerned.

davidelang, 2019-09-03:
thanks, I'm also thinking of the 8' range, so good to know that works.

I'm primarily thinking in terms of squaring up the machine. If it's parallel to
0.1mm, that's much more accurate than you will get from a tape measure. It's
probably more accurate than your positioning of the microswitches as well :-)

I don't think that you are really going to be able to do any better than a 1/2
step in any case (yes, a microswitch can detect smaller distances, but you
aren't going to be able to control the machine accurately to that precision)

David Lang

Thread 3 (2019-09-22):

powered makerbot style endstop support

thawkins, 2019-09-22:
If you find yourself laying out a new revision, can you add support for powered end stops, these are very common on 3D printers and can be had for pennies, they include all the filters at the switch end and have an LED for confirming operation.

see: http://marlinfw.org/assets/images/docs/hardware/endstops/makerbot_endstop.png

The only requirement, is to add an extra +5v pin on the end-stop pin-outs, so that each end-stop row has

[Signal] - [Grnd] - [Vcc]  as per the RAMPS cards

Typical prices are very very low.

here is a listing from my region, but these devices can be found everywhere

https://www.lazada.com.ph/products/6pcs-mechanical-endstop-limit-switch-press-switch-module-for-3d-printer-makerbot-prusa-mendel-reprap-cnc-arduino-mega-2560-1280-ra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

the price here for 6 pre-wired end-stops is about $3

bdring, 2019-09-22:
Have you tried using those with 3.3v? The resistor is pretty high, so they might not light up. 5V will kill an ESP32

thawkins, 2019-09-22:
I will have a play next week i have a couple of esp32, i can breadboard on 3.3v with these switches  if i can hook one up to a gpio and see if i can read them with a 3.3v Vcc.  I will also be able to see what the led briteness is like.

bdring, 2019-09-22:
I have used these switches. They work fine for close on contact if you use the red and white wires. They will light up at 3.3V. The resistor appears to be 810R, but very hard to read.

[They are common on amazon](https://www.amazon.com/gp/product/B07PCN6T6F)

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

thawkins, 2019-10-17:
I have confirmed that these style endstop boards work fine at 3.3v, in fact i cant really tell the difference between 5v and 3.3v operation, the leds seem equaly bright.

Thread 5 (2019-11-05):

Non-MPCNC use

vertiginous, 2019-11-05:
Apologies if this isn't the right place to ask this question.

I want to use grbl_esp32 to control an openbuilds ox CNC router that I'm building.  It will need a single driver for x and z, and 2 drivers for Y.  Also, not sure it's relevant, but I plan to use TMC2130 drivers, as I believe I'll need the additional current for my motors.

I found the grbl_ESP32_MPCNC controller card on tindie, and I think it can do what I want.  I don't want to use auto-squaring or have a ganged x axis, so can I just comment out the extra x step pins and the x and y axis squaring in cpu_map.h?

```
#define USE_GANGED_AXES // allow two motors on an axis

  #define X_STEP_PIN      GPIO_NUM_12
  // #define X_STEP_B_PIN    GPIO_NUM_22  // ganged motor
  // #define X_AXIS_SQUARING

  #define Y_STEP_PIN      GPIO_NUM_14
  #define Y_STEP_B_PIN    GPIO_NUM_21  // ganged motor
  // #define Y_AXIS_SQUARING

  #define Z_STEP_PIN      GPIO_NUM_27

  #define X_DIRECTION_PIN   GPIO_NUM_26
  #define Y_DIRECTION_PIN   GPIO_NUM_25
  #define Z_DIRECTION_PIN   GPIO_NUM_33

  // OK to comment out to use pin for other features
  #define STEPPERS_DISABLE_PIN GPIO_NUM_13
```

bdring, 2019-11-05:
It should work, so if it does not, I'll fix it.

I won't be able to try it until late tomorrow

vertiginous, 2019-11-21:
In my initial post I mentioned I was going to use TMC2130's, but I was confused.  I actually ordered TMC5160 v1.2 drivers.   I was under the impression they were supported, but I got firmware support confused with support on this specific controller board.

I have received my mpcnc controller from tindie, and I have it working with a few stepper motors and a4988 drivers.  When i plug in the TMC5160 drivers, the motors don't move.  I was under the impression these could be run in step\dir mode without any changes, but these boards are in SPI mode, and I've found no information on how to change them.

My next thought was that I could add a few lines to my cpu_map and use SPI mode, and then after further reading I realized this board isn't designed for SPI mode.

I also considered using jumpers between the drivers and using the unused (in my case) X_STEP_B pin for the X_CS_PIN.  Now after another look at the schematic, I see that 3.3v is connected to those pins, so I'm thinking that won't work either.  I could use a little guidance if this combination of controller board and drivers is possible.

Thanks!

bdring, 2019-11-21:
The MPCNC controller does not support SPI mode.

The ESP32 is very flexible, but limited in I/O pin count. It is hard to support too many options on a PCB, especially with 5 stepper drivers.

An MPCNC controller with SPI could be designed. I would suggest using SPI daisy chained drivers to reduce the number of pins required.

vertiginous, 2019-11-21:
OK, these drivers came with daisy chain jumpers, and I was hoping since I'm only using 4 drivers I could get creative with robbing pins from elsewhere.  I think the answer I'm looking for is somewhere between the mpcnc board and the 4 axis SPI board.  Thanks for your time!

bdring, 2019-11-21:
You could use those inverted pins to make it work. It would require soldering, but not cutting of traces.

You would need to repurpose a pin for the CS, like spindle enable. You would have to figure it our on your own, because I don't want to create a support problem for myself.

Bottom line: Grbl_ESP32 can do just about anything you need, but when you commit to copper, you need to make some permanent choices

vertiginous, 2019-11-22:
I don't think my soldering skills are up to the task.  I'm going to go with TMC2209's. They're working fine with no modifications.  Thanks again.  I learned a great deal from this exchange.

Closed 2019-11-22.

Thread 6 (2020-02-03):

Dual endstops per axis?

tortfeaser, 2020-02-03:
Hi, thanks for this design.

I've just pushed the button for an order from JLCPCB then noticed J3 doesn't allow for separate limit switches for separate motors on X and Y axes? Does Grbl allow for this? I was hoping to run this board on a V1 Engineering Lowrider where separate minimum limit switches for each of the two X axis rails to allow for autosquaring (and same on Z min).

Am I talking nonsense? Or does Grbl (unlike Marlin) not allow for two limit switches for each X motor?

tortfeaser, 2020-02-04:
Sorry. Just realised this is a dumb question. Two switches are connected and the firmware moves one motor at a time and waits for one of the switches to trigger.

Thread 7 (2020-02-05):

A-Axis Configuration

mckeeler, 2020-02-05:
I recently purchased one of your MPCNC boards and it is working well.
If I wanted to use the Y-axis as an A-Axis for rotation how would it be configured in GRBL ESP32
Would I be able to command angular degrees? and how would the feed rate be calculated if there was a linear and rotary movement on the same line?

bdring, 2020-02-05:
Can you draw a quick sketch or markup a picture of the controller of exactly what you want each stepper motor to do?

The resolution setting controls the step to units, so you can have that be degrees. Are you working in millimeters or inches?

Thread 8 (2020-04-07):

Joint use of a relay and a PWM laser

maximius, 2020-04-07:
Repeated the grbl_esp 32_cnc_controller v1.2.1 Board. I Use a CNC engraver with the ability to connect a milling cutter and a laser. When using the relay to switch the router in the firmware we use pin 2 and the string
#define USE_SPINDLE_RELAY
to connect the laser to the PWM we use pin 17 and a string
//#define USE_SPINDLE_RELAY

Is it possible to configure the firmware so that the PWM is sent to pin 17, and the relay connected to pin 2 switched the relay simultaneously, without updating the esp32 firmware?
changing the parameter $32 (laser mode) changes only the strategy of switching on the relay, but not its pin.
This is important for combined processing on CNC machines. Thank you for any help.

maximius, 2020-04-07:
Good afternoon. Is it planned to implement the function of disabling the relay output when turning on laser mode $32=1

bdring, 2020-04-07:
You could use the spindle enable pin for the relay.

`#define SPINDLE_ENABLE_PIN      GPIO_NUM_2`

maximius, 2020-04-07:
I tried this option. When it is in the mode $32=0, the spindle works as it should, but

when entering the parameter $32=1 and flashing the code
//#define USE_SPINDLE_RELAY

#ifdef USE_SPINDLE_RELAY
#ifdef V1P1
#define SPINDLE_PWM_PIN GPIO_NUM_17
#else // V1p2
#define SPINDLE_PWM_PIN GPIO_NUM_2
#endif
#else
#define SPINDLE_PWM_PIN GPIO_NUM_16
#define SPINDLE_ENABLE_PIN GPIO_NUM_2
#endif

the relay is often switched on/off, but there is no PWM signal at output 16. If

//#define USE_SPINDLE_RELAY

#ifdef USE_SPINDLE_RELAY
#ifdef V1P1
#define SPINDLE_PWM_PIN GPIO_NUM_17
#else // V1p2
#define SPINDLE_PWM_PIN GPIO_NUM_2
#endif
#else
#define SPINDLE_PWM_PIN GPIO_NUM_16
#define SPINDLE_ENABLE_PIN GPIO_NUM_32
#endif

the PWM signal on the pwm output (pin 16) works as it should.

bdring, 2020-04-07:
I might be able to write a custom machine definition file.

It would help to know exactly what you are trying to do and why.

Cows2Computers, 2020-07-08:
On the lowrider machine, allot of people have both a spindle and laser mounted at the same time. It would be nice to have the relay for turning on the spindle and PWM to run the laser. You would just then not supply source power to whichever tool you are not using.

Spacejamairways, 2023-11-07:
I made this well i tried 3 methods with videos. Linked pt1 https://youtube.com/shorts/0fDZFcwfVqU?si=npPupSD3e--cxUIT

Pt2 and coming. I burned my little red stepper driver and  I have tried to use one blue relay and then I tried 1 blue relay controlling a regulator big relay and then that didn't work so I tried high and low trigger relay which really didn't work . Going thru drivers alot hahah

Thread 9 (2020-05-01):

Fan pin - faulty ground pin

indimini, 2020-05-01:
Hi,

I just received my board and have grbl software installed on ESP32.  I have power to each of the stepper controllers,  but probing the fan pins w my multi-meter I see 0 V. if I move the gnd probe to the input power Gnd, and keep the + probe on the fan +5V pin, I see 4.95 V.

Is there a config setting I need to change in a .h file to get the fan post to work, or is this a fault in the PCB?

bdring, 2020-05-01:
The connector should be permanently connected to %V and Gnd. Can you check the solder connection on the back of the board?

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

indimini, 2020-05-01:
Visual inspection doesn't show anything obvious. If I check continuity from the solder joint on the board it still indicates a broken connection.

indimini, 2020-05-03:
I had no luck with getting gnd on that pin to work by resoldering, so I just soldered a jumper cable from the pin to the input gnd.  Looking at the picture above, it doesn't look like the fan gnd is connected to the input gnd - is that just on a different layer?

bdring, 2020-05-03:
There are only 2 layer. The bottom reddish layer is mostly a ground plane.  I do limited testing on each board, but every one gets a power supply test. I put power in the input terminal block and measure the output with a meter on those pins.

indimini, 2020-05-03:
The hard-wired jumper seems like it will work.  There was definitely no voltage across the pins prior to putting in the jumper.  Not a big deal - just thought I'd confirm it wasn't just a software config item before I broke out the soldering iron. :)  The rest of my tests have gone great.  I really appreciate you putting out this board as I was never a fan of Marlin for the CNC and this was a huge move forward.

bdring, 2020-05-03:
Sometimes those little pins have trouble soldering to a heavy ground plane.

Closed 2020-05-23.

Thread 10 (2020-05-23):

Error notice: Fan ground pin.

bdring, 2020-05-23:
The most recent version of the board has a missing connection on the fan pin. To use a fan you will have to pick up a ground somewhere else or solder a wire to the primary ground.

Sorry about that.

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

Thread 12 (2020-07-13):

Questions/Issues re: homing

indimini, 2020-07-13:
I am trying to get the homing/squaring functions sorted out but am having some issues.  (I am only working with one axis at a time,  in this case, the X-axis.)  I have the steppers and limit switches wired up - movement to home is in the +X axis.  When I click on the Home X, the steppers run, the limit switches both trigger, but only one side will back off and reset the switch.  The other side will attempt to move in the +X direction and not back off from the closed limit switch. (The switches are wired as NC, so when closed, a continuity check shows no signal.)  Any insights on what I'm doing wrong or where my configuration needs adjustment would be appreciated.

bdring, 2020-07-13:
Start by making sure the switches are reading properly. Use this wiki page.

https://github.com/bdring/Grbl_Esp32/wiki/Help-with-Switch-Problems

indimini, 2020-07-16:
I've checked my switches and they work as expected.  Ensuring that the #10 bit 4 is set, if I run '?' I confirm that the pins work as expected.  When I home an axis (X for example), the gantry moves toward the limit switches, both switches trigger, the gantry backs off a bit then moves forward again.  At that point, one stepper motor will back off but the other stepper tries to move forward into the limiter.  It seems as if the instructions to back off is inverted for one o the two stepper motors.

bdring, 2020-07-16:
It might be easiest if we work together on this via slack. Is there a good time tomorrow? My day is open except after 5pm US central time

indimini, 2020-07-16:
That would be great, thanks!  I am East coast, I my only hard obligation is from 11 to 12 pm.  Let me know how to connect on Slack.

To add a bit more detail, whichever switch is triggered first is the one which will continue to move forward after first backing off the switch. The error is Alarm 6 - Homing fail. The active homing cycle was reset.  I've tried adjusting homing debounce (both increasing and decreasing) as well as the homing pull of (again increasing and decreasing) with no success.

Here's a summary of what I see on the status window for Pn:
Pn:YZ
Pn:YZ|WCO:10.000,0.000,0.000
Pn:XYZ|Ov:100,100,100
Pn:YZ
At that point, one stepper keeps moving in the wrong direction, triggering the ALARM 6: Homing fail. The active homing cycle was reset

indimini, 2020-07-21:
Are you still available sometime to track down this issue?  I have now confirmed the same behavior on both X and Y axis homing attempts.

bdring, 2020-07-21:
Yes, I live in the US Central time zone. Suggest a few reasonable times that work for you and we can interact on Slack.

indimini, 2020-07-22:
If you have time this Thurs or Fri between 11 am and 4 pm CT, that would work.  I can also do something later on Thursday.

bdring, 2020-07-22:
Friday at 2:00pm US Central time will work for me. Just have the machine ready to go and we can trouble shoot together.

indimini, 2020-07-22:
Great - how can I find you on slack?

bdring, 2020-07-22:
[Slack Link](https://join.slack.com/t/buildlog/shared_invite/zt-7twbithi-bRGScOaCgJoBpTbkykfxoA)

I will close this task after I see you join.

Closed 2020-07-22.

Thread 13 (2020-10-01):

Probe usage issue

matuskasinec, 2020-10-01:
Hi, I am new to CNC and programming as well. I am trying to figure out how to use the probe to set zero prior to starting main program.
I have created a simple program that was given on V1 engineering:
G92 X0 Y0 Z0 ; Set Current position to 0, all axes
G00 Z5.0000 F500.0 ; Raise Z 5mm at 8.3mm/s to clear clamps and screws
G28 Z-60 F40 ; Home in order, w/zprobe
M00
G92 Z0.15 ; Account for probe thickness (set your thickness)
G00 Z5.0000 F500 ; Raise Z probe off off of surface
M00 ; pause for LCD button press
M03 S<s> ; PID, set spindle speed

Challange1: During the G28 line the z-axis moves at a lot higher speed than F40.
Challange2: During the movement on G28 when the Prb pin connects to the ground Pin nothing happens.
Challange3: M03 does not engage the spindle relay.

I am wondering what I am doing wrong here.
Thank you

bdring, 2020-10-02:
I don't know of a way to do it. It seems dangerous  to integrate probing into the start of a job.

G92 is not good practice. It is not saved, so it cannot be recalled later. It it better to use [G10 L20 X0 Y0 Z0](https://linuxcnc.org/docs/2.6/html/gcode/gcode.html#sec:G10-L20) to set the current work coordinate system to 0,0,0.

[G28](https://linuxcnc.org/docs/2.6/html/gcode/gcode.html#sec:G28-G28_1) is always a rapid move.

Probing is done with [G38](https://linuxcnc.org/docs/2.6/html/gcode/gcode.html#sec:G38-probe)

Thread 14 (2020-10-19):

How is the spindle relay being activated?

hgruber, 2020-10-19:
I got this far with this whole project (homing, plotting, ..), but I couldn't figure out how to enable/disable the spindle relay in grblesp. USE_SPINDLE_RELAY is defined in mpcnc_v1p2.h, but whatever M-code I use, the relay does not respond. It must be something stupid and simple...

thanks for any quick help

bdring, 2020-10-19:
Use the most current version of the main or devt (beta) branches of the firmware. Use mpcnc_v1p2.h as your machine definition file.

In that file uncomment **#define USE_SPINDLE_RELAY**.

After loading the firmware send **$Spindle/Type=RELAY** from the serial port of WebUI console. This only needs to be done once.

You should be able to activate the spindle relay with M3 S1 when in the idle state. If that does not work, please paste your startup messages here to help me debug. We can also help you in real time via Slack.

hgruber, 2020-10-22:
Okay, thanks, perfect.
I also had to update to FW: 1.3a (20201004)
At first I thought homing was broken, only to find that it is even better.
Thanks for all that work, I really appreciate it!

Closed 2020-10-22.

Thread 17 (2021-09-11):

port of your schematic

linewallker, 2021-09-11:
Hello,
  Some time ago I was trying to find ESP 32 CNC shield to buy and I found your schematic on the GITHUB so I downloaded your schematic and made some changes in it for my personal purposes.

Can I ask you for checking my schematic if it will be compatibile with your firmware ?

https://github.com/linewallker/ESP-32-CNC-SHIELD-PORT

If not I understnad.

Thank you for any kind of answer.

linewallker, 2021-09-24:
Hello, I am still waiting for your response.

bdring, 2021-09-24:
Sorry, I was on vacation when this message arrived. Please ask this
question on our  public channels of our Discord server. Please post a PDF
of the schematic and describe the changes you made. Also post a PDF of the
layout.

https://discord.gg/ArD5rPruKt

On Fri, Sep 24, 2021 at 8:39 AM linewallker ***@***.***>
wrote:

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

--
Bart Dring

"If you did not build it, you will never own it"

linewallker, 2021-09-26:
Hello,
  I have added Esp32_shield.pdf into repository with schematics.

Basicly I have made only small changes in one of your designs.

I have removed SD card because I am using big laser engraver 120 cm x 135 cm for photo engarving in full size and it makes files bigger than 2 gb so it is better to stream from PC.

I have cloned X and Y sockets for drivers, but not for independt driving of each motor, only created another socket with same connection as old one.

I have added pinout for external rellay, I have conected to EN circuit to take out signal for turn On and Off the rellay when the mottors are running, using for Air Assist compressor for 220V, I have already tested this connection on Arduino CNC shield connected to EN pin on unused Z axis and it is working fine with ferite filter on wiring to the rellay from shield.

Also I have alternated the connections on PCB but strictly kept your pinouts.

I hope this description is Ok for you :)

linewallker, 2021-09-26:
If you send me an email, I will share to you link on Altium Circuitmaker so you can see the full view if you want ;)

linewallker, 2021-09-26:
Try this :
https://365.altium.com/files/C485A942-C92D-11EB-A2F6-0A0ABF5AFC1B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

linewallker, 2021-09-28:
I have Updated detailed PDF file with schematics few minutes ago, I hope this will help.

https://github.com/linewallker/ESP-32-CNC-SHIELD-PORT/blob/main/esp32_shield.pdf

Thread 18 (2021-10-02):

Issue in BOM "BOM_MPCNC Vp1p2p2.xlsx"

tchleb, 2021-10-02:
Hi, there is an issue at the BOM "BOM_MPCNC Vp1p2p2.xlsx"
Transistor Q1 is the wrong type.

**BOM_MPCNC Vp1p2p2.xlsx --> Q1 == BCV26 (PNP)**

**MPCNC_V1P2P1_bom.csv --> Q1 == MMBT9013H (NPN)**

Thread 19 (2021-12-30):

PWM Voltage Drop

P90Alex, 2021-12-30:
I am Using V1.2.1 on an MPCNC using the latest grbl esp32 firmware with the mpcnc_laser_module_ v1p2.h machine.  I am using JTech 2.8W laser and I am having issues with the PWM output.  When I read the voltage across the PWM pins and NO wires attached to these pins, with M3S1000 command, I read 5v but when I attach the JTech driver board to these pins then the voltage drops to around 2.6v with the same M3S1000 command.  Has anyone else had this issue or know what the cause for it is?

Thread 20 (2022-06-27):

Connection stop button

IgorPack, 2022-06-27:
Hey,

Please tell me how to properly connect the Stop button to this controller, the button itself is normal, connecting to the contact Pst, Srt and Hold do not give results? What am I doing wrong?

Thanks.

Closed 2022-07-15.

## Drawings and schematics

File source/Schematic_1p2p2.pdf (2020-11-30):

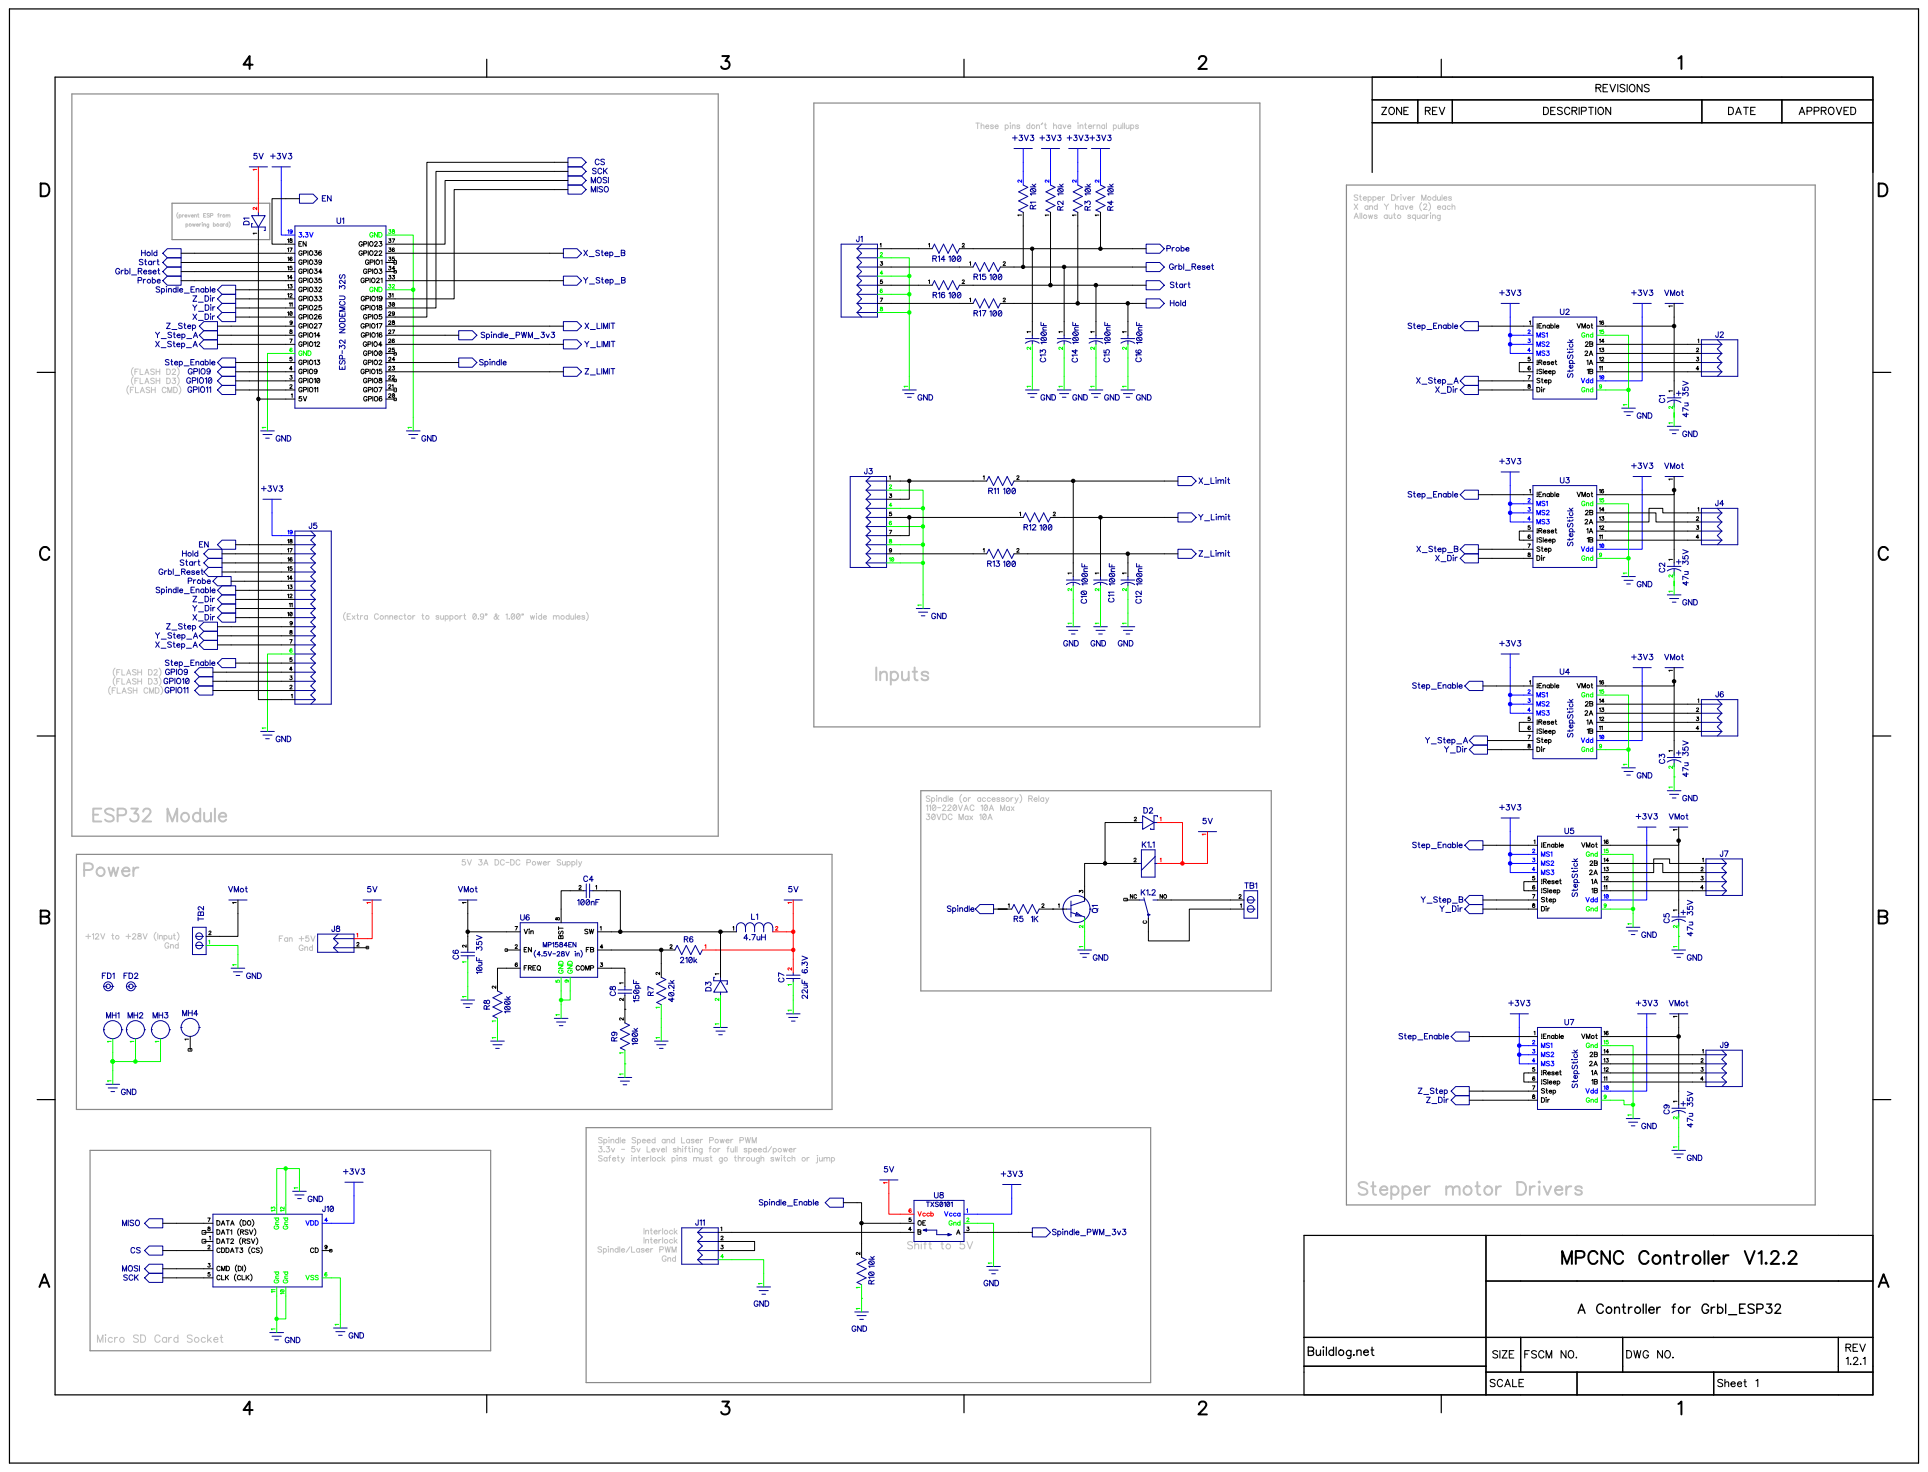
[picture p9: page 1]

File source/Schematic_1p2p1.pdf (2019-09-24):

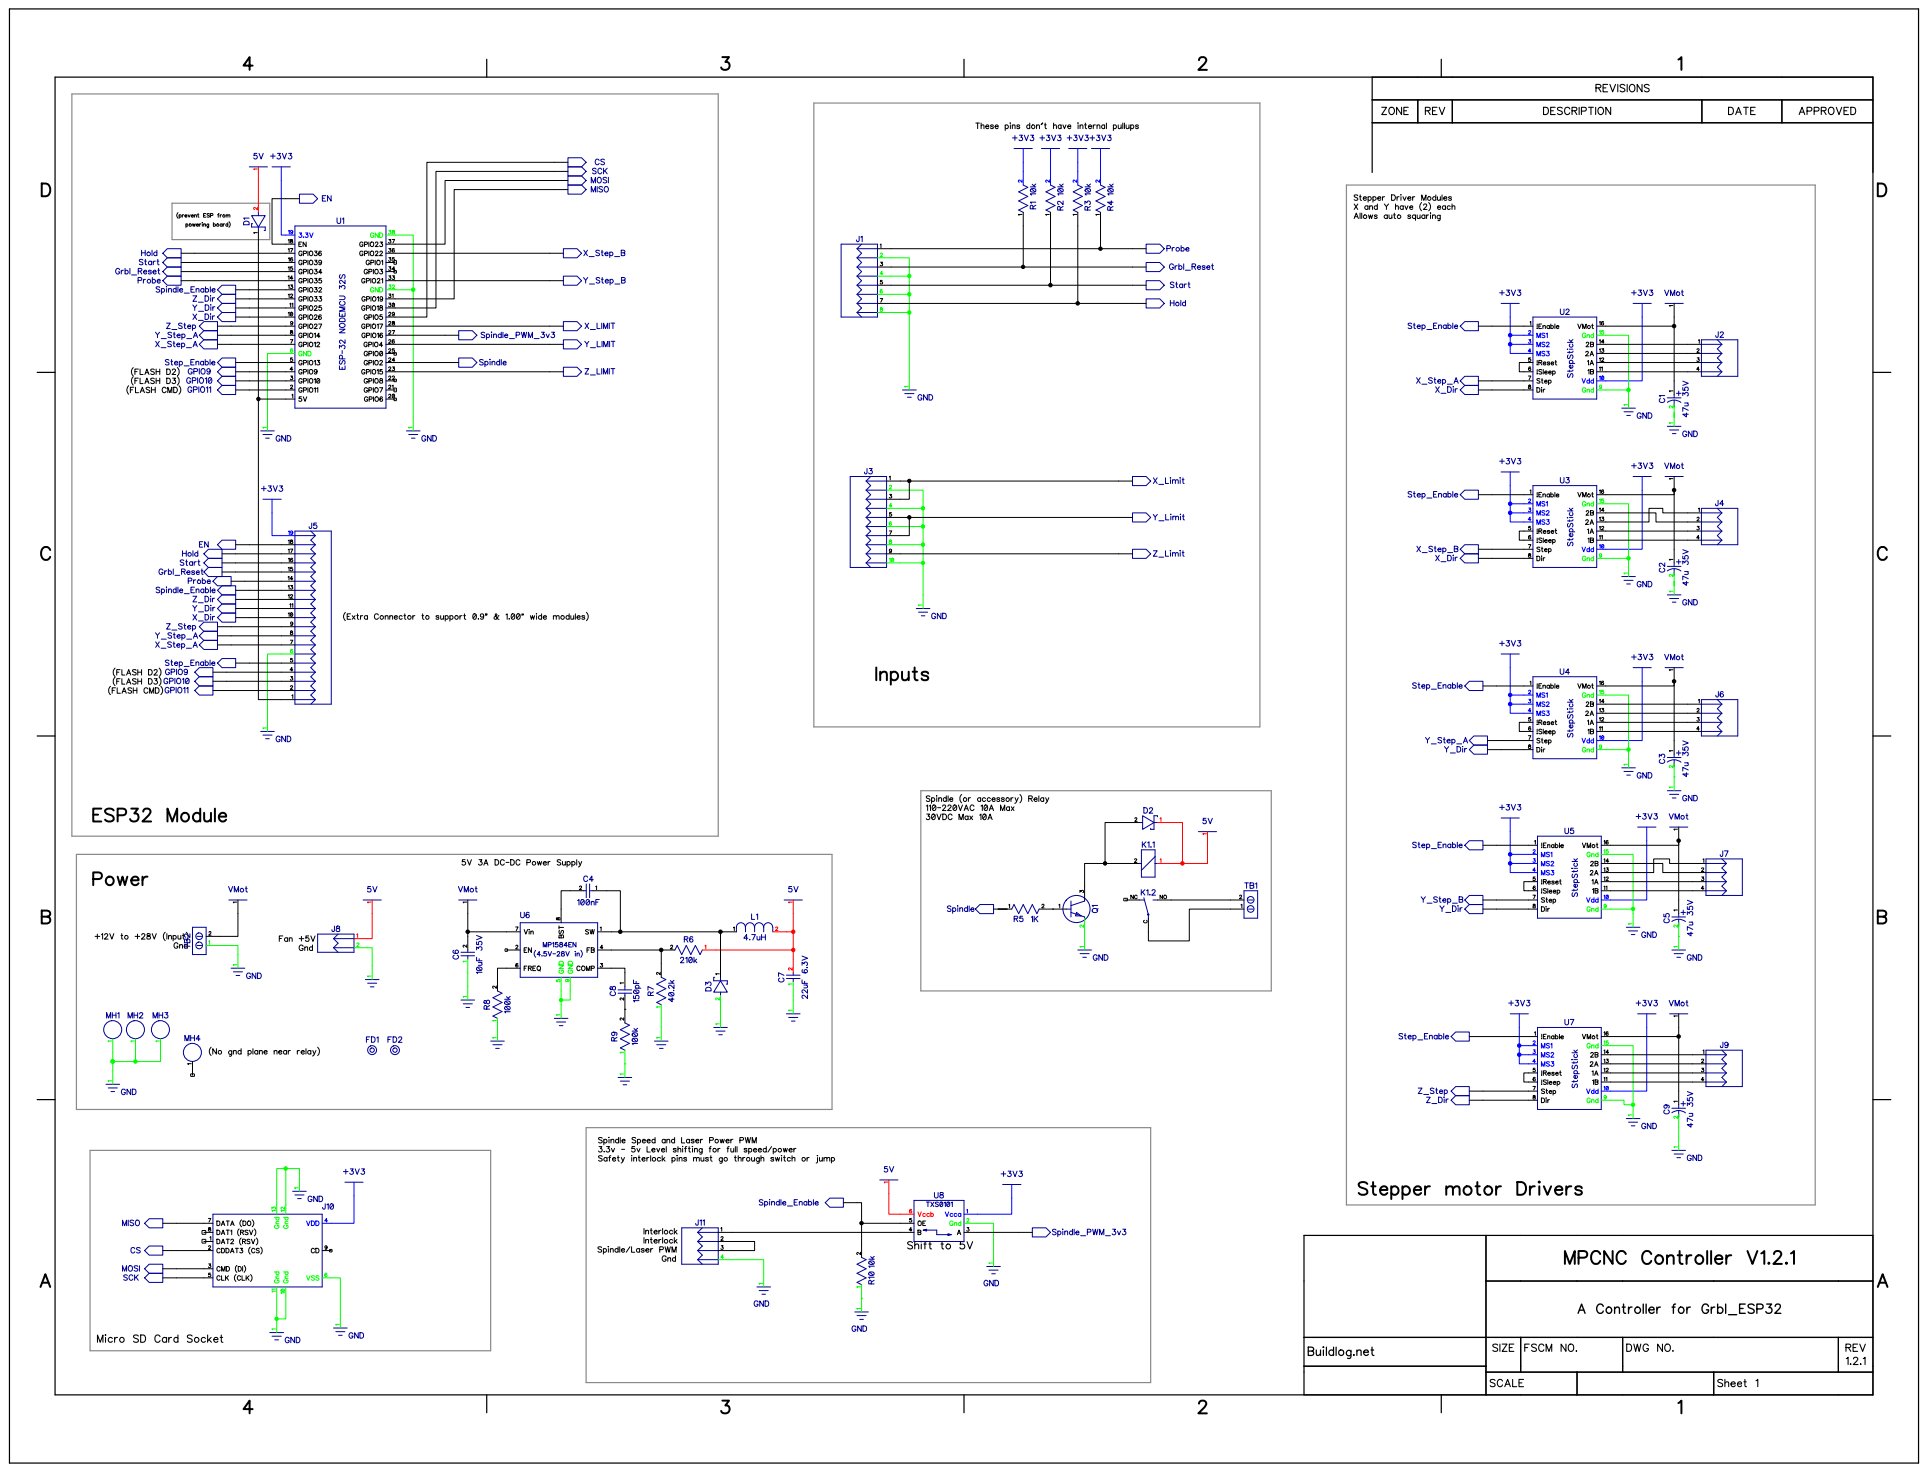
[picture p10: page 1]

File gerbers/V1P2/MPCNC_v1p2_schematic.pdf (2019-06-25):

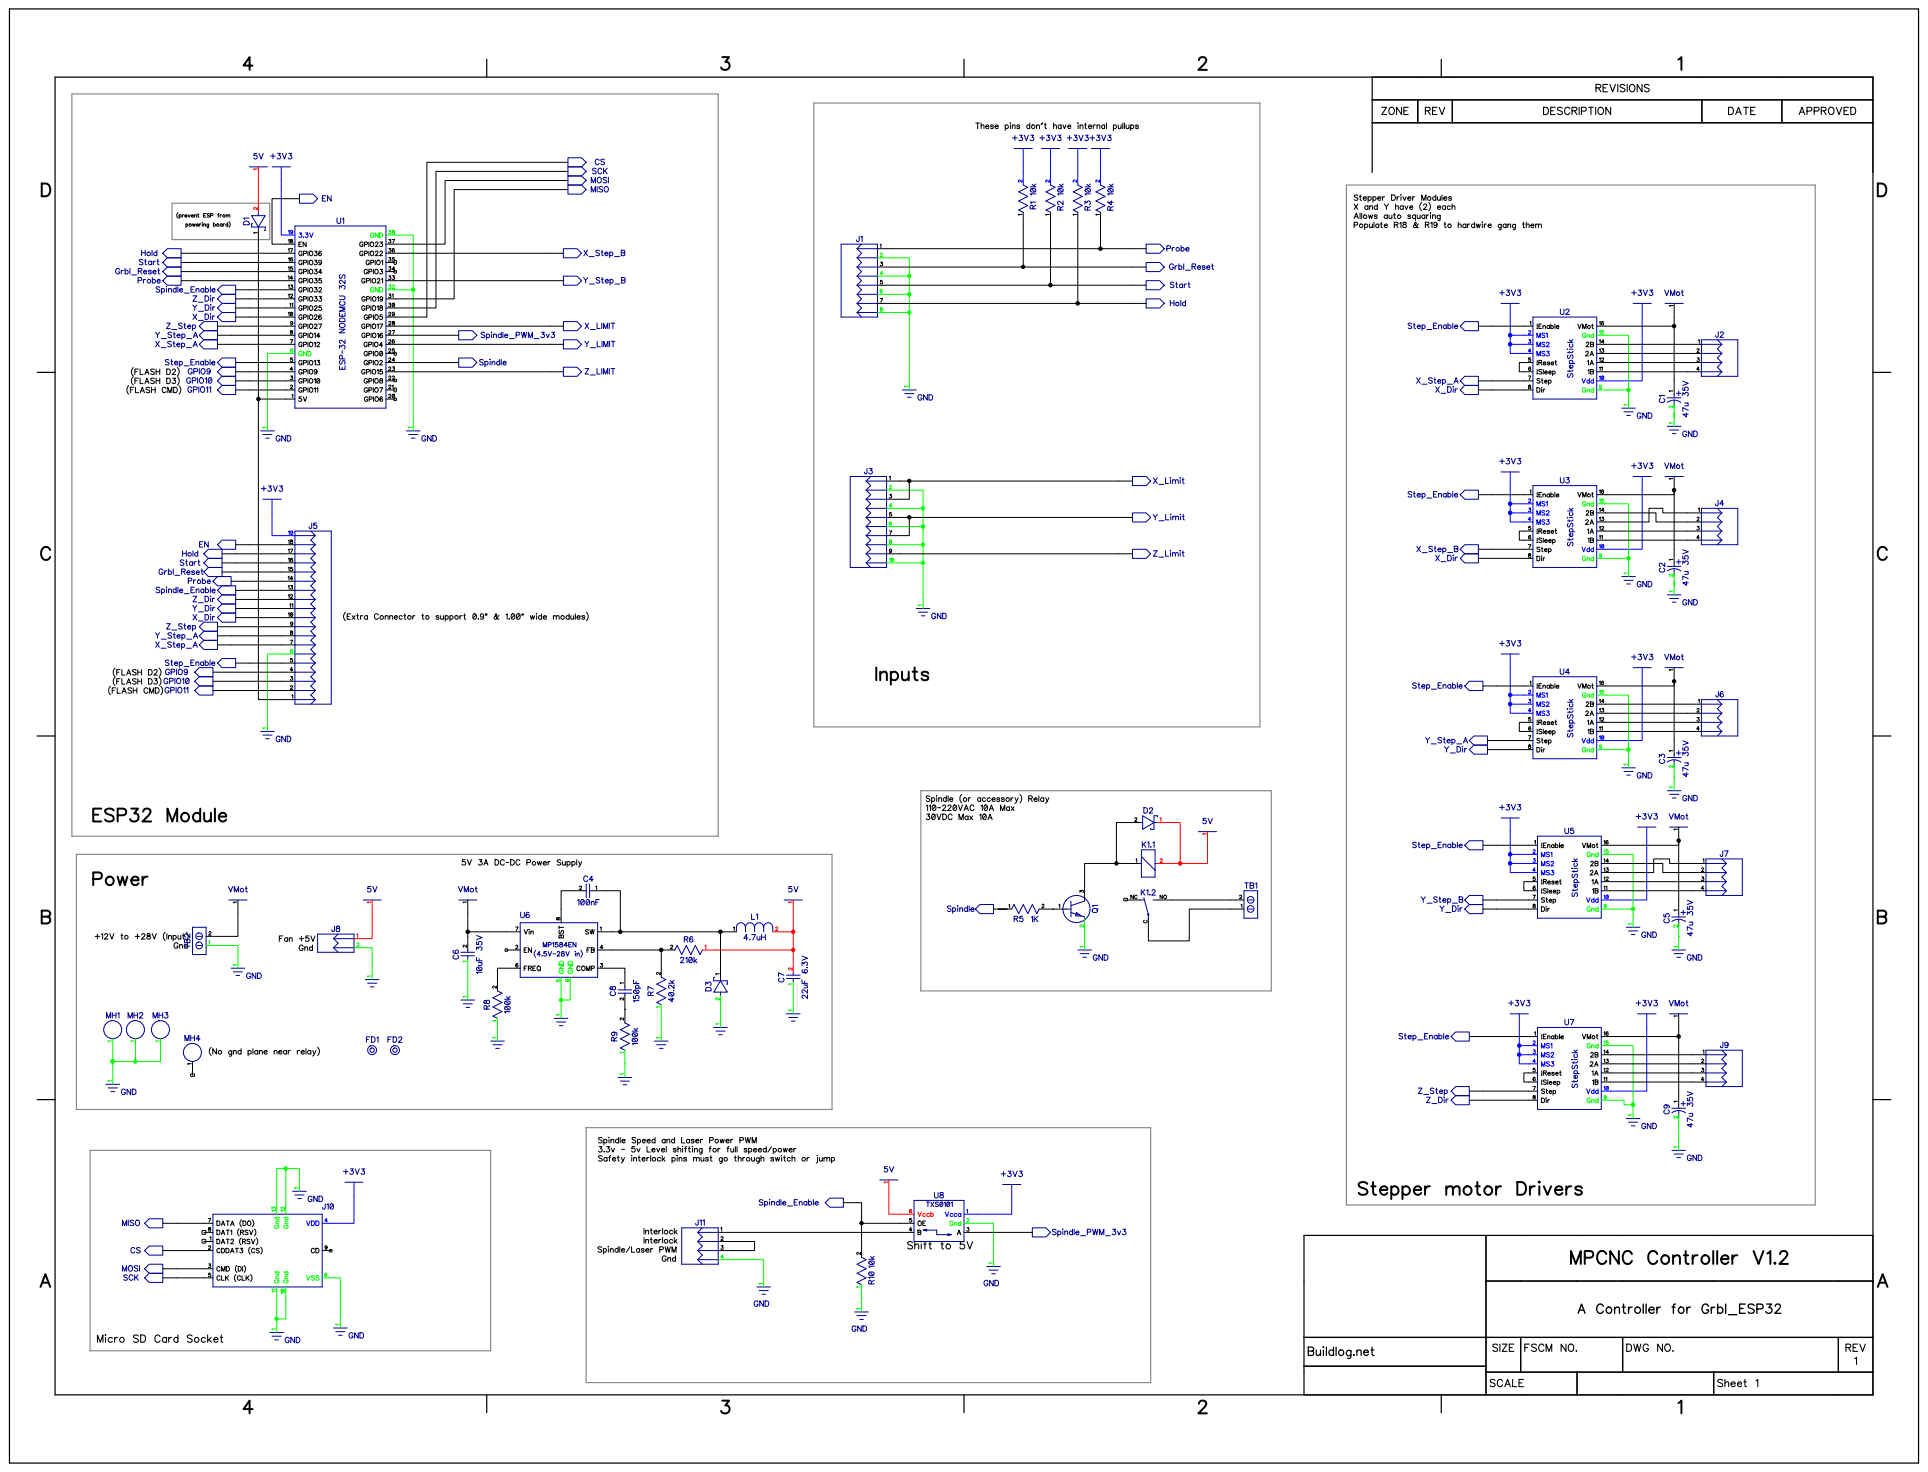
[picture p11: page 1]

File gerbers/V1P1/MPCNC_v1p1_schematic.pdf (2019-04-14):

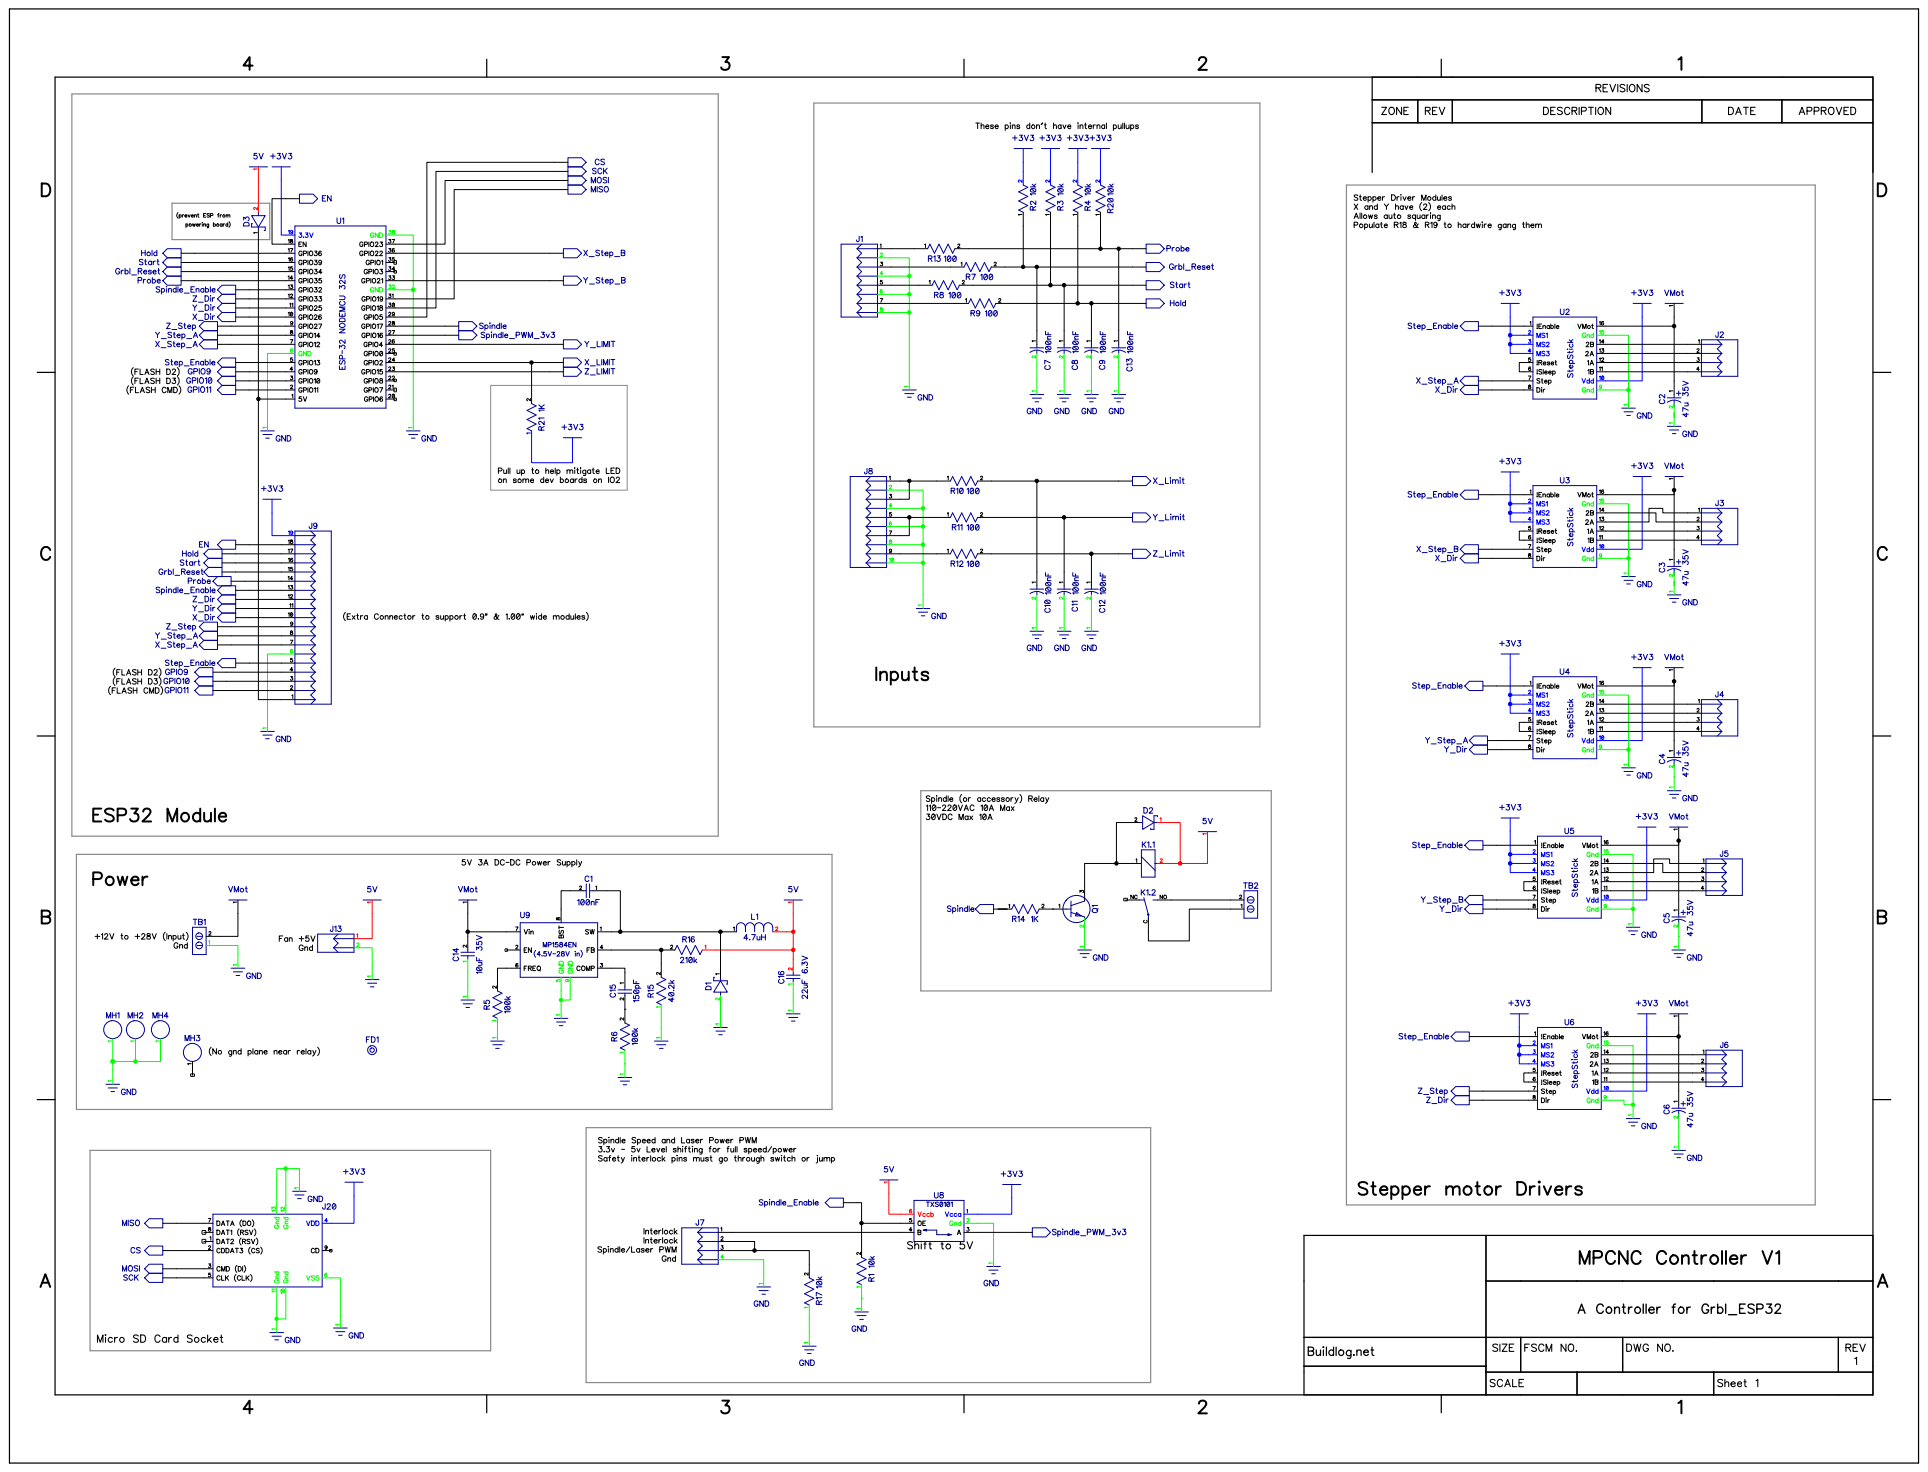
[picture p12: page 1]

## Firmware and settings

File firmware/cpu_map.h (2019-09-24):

#ifdef CPU_MAP_MPCNC  // all versions...select below
	// This is the CPU Map for the Buildlog.net MPCNC controller
	
	// uncomment ONE of the following versions
	//#define V1P1
	#define V1P2  // works for V1.2.1 as well
		
	#ifdef V1P1
		#define CPU_MAP_NAME "CPU_MAP_MPCNC_V1P1"
	#else // V1P2
		#define CPU_MAP_NAME "CPU_MAP_MPCNC_V1P2"
	#endif	
		
	// switch to the correct default settings
	#ifdef DEFAULTS_GENERIC
		#undef DEFAULTS_GENERIC
	#endif
	#define DEFAULTS_MPCNC
	
	#define USE_GANGED_AXES // allow two motors on an axis 
  
	#define X_STEP_PIN      GPIO_NUM_12
	#define X_STEP_B_PIN    GPIO_NUM_22	 // ganged motor
	#define X_AXIS_SQUARING
	
	#define Y_STEP_PIN      GPIO_NUM_14
	#define Y_STEP_B_PIN    GPIO_NUM_21  // ganged motor
	#define Y_AXIS_SQUARING
	
	#define Z_STEP_PIN      GPIO_NUM_27
	
	#define X_DIRECTION_PIN   GPIO_NUM_26
	#define Y_DIRECTION_PIN   GPIO_NUM_25  
	#define Z_DIRECTION_PIN   GPIO_NUM_33 
	
	// OK to comment out to use pin for other features
	#define STEPPERS_DISABLE_PIN GPIO_NUM_13				
				
	// Note: if you use PWM rather than relay, you could map GPIO_NUM_2 to mist or flood 
	//#define USE_SPINDLE_RELAY
	
	#ifdef USE_SPINDLE_RELAY
		#ifdef V1P1
			#define SPINDLE_PWM_PIN    GPIO_NUM_17
		#else // V1p2
			#define SPINDLE_PWM_PIN    GPIO_NUM_2
		#endif			
	#else
		#define SPINDLE_PWM_PIN    GPIO_NUM_16
		#define SPINDLE_ENABLE_PIN	GPIO_NUM_32
	#endif
	
	#define SPINDLE_PWM_CHANNEL 0
	// PWM Generator is based on 80,000,000 Hz counter
	// Therefor the freq determines the resolution
	// 80,000,000 / freq = max resolution
	// For 5000 that is 80,000,000 / 5000 = 16000 
	// round down to nearest bit count for SPINDLE_PWM_MAX_VALUE = 13bits (8192)
	#define SPINDLE_PWM_BASE_FREQ 5000 // Hz
	#define SPINDLE_PWM_BIT_PRECISION 8   // be sure to match this with SPINDLE_PWM_MAX_VALUE
	#define SPINDLE_PWM_OFF_VALUE     0
	#define SPINDLE_PWM_MAX_VALUE     255 // (2^SPINDLE_PWM_BIT_PRECISION)
	
	#ifndef SPINDLE_PWM_MIN_VALUE
			#define SPINDLE_PWM_MIN_VALUE   1   // Must be greater than zero.
	#endif
	
	#define SPINDLE_PWM_RANGE         (SPINDLE_PWM_MAX_VALUE-SPINDLE_PWM_MIN_VALUE)		
	
	// Note: Only uncomment this if USE_SPINDLE_RELAY is commented out.
	// Relay can be used for spindle or either coolant
	//#define COOLANT_FLOOD_PIN 	GPIO_NUM_2
	//#define COOLANT_MIST_PIN   	GPIO_NUM_2
	
	#ifdef V1P1	//v1p1
		#define X_LIMIT_PIN      	GPIO_NUM_2
	#else
		#define X_LIMIT_PIN      	GPIO_NUM_17
	#endif	
	
	#define Y_LIMIT_PIN      	GPIO_NUM_4  
	#define Z_LIMIT_PIN     	GPIO_NUM_15 	
	#define LIMIT_MASK      	B111
	
	#ifdef V1P2
		#ifndef ENABLE_SOFTWARE_DEBOUNCE   // V1P2 does not have R/C filters
			#define ENABLE_SOFTWARE_DEBOUNCE
		#endif
	#endif
	
	#define PROBE_PIN       	GPIO_NUM_35  
	
	// The default value in config.h is wrong for this controller
	#ifdef INVERT_CONTROL_PIN_MASK
		#undef INVERT_CONTROL_PIN_MASK			
	#endif
	
	#define INVERT_CONTROL_PIN_MASK   B1110
	
	// Note: default is #define IGNORE_CONTROL_PINS in config.h
	// uncomment to these lines to use them		
	#ifdef IGNORE_CONTROL_PINS
		#undef IGNORE_CONTROL_PINS
	#endif
	
	#define CONTROL_RESET_PIN         GPIO_NUM_34  // needs external pullup
	#define CONTROL_FEED_HOLD_PIN     GPIO_NUM_36  // needs external pullup 
	#define CONTROL_CYCLE_START_PIN   GPIO_NUM_39  // needs external pullup    		
		
#endif

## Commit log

2019-04-14 First Push
    [MPCNC_bom.csv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]
2019-04-20 Added sample gcode
    A sample for testing the SD card
2019-05-01 Added STL of Fan Mount
    [mpcnc_fan_mount.stl]
2019-06-25 Add V1P2 and reorganize files
    - Version 1.2 added
    - Reorganize files to clarify versions
    [MPCNC_V1P1_bom.csv, MPCNC_V1P2_bom.csv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]
2019-06-30 Fixed BOM Error
    - C5 was missing
    [MPCNC_V1P2_bom.csv]
2019-09-24 Adding version 1.2.1 files.
    [MPCNC_V1P2P1_bom.csv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]
2020-07-08 Add files for case
    Added files for a case. Lid with and without 7mm holes for switches. Base with and without standoffs for use on the Lowrider.
    [Grbl_ESP-32 MPCNC Case Flat Base.stl, Grbl_ESP-32 MPCNC Case Lid Holes.stl, Grbl_ESP-32 MPCNC Case Lid.stl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]
2020-11-12 Added STLs
    [DINRailClip.stl, GRBLESP32MPCNCDinRailPlate.stl]
2020-11-30 Add V1p2p2
    [BOM_MPCNC Vp1p2p2.xlsx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]
2022-03-09 Moved files
    [BOM_MPCNC Vp1p2p2.xlsx, placement.csv]
